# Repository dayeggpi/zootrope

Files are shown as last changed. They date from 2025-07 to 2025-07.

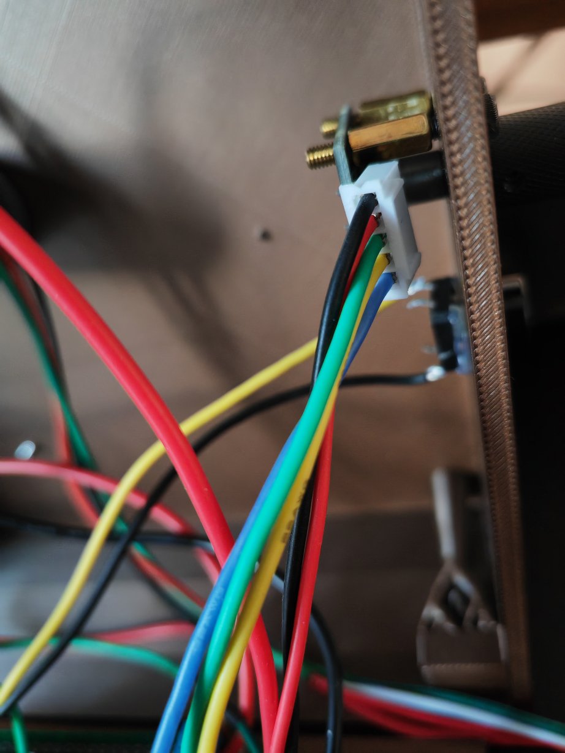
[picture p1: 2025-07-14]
images/rotary-wiring.jpg

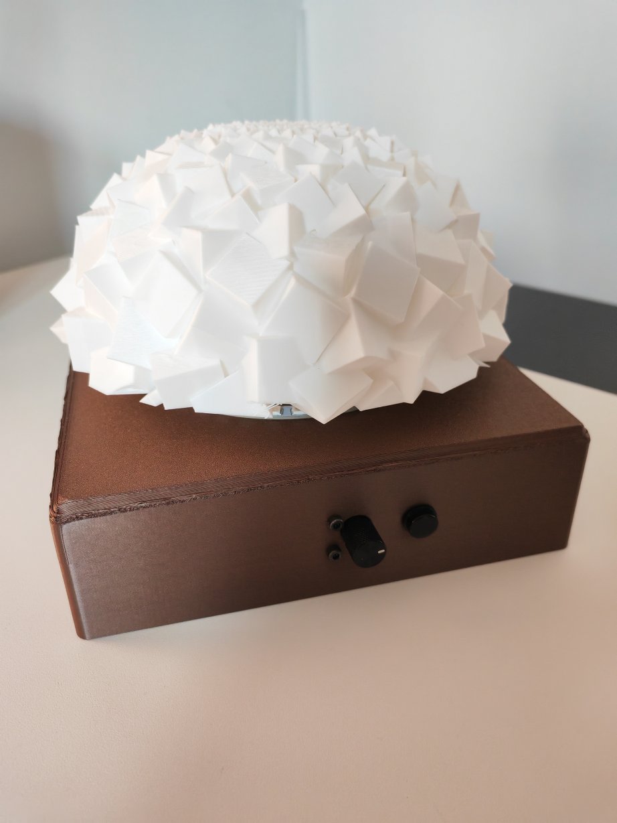
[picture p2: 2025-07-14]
images/final.jpg

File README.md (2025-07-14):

# zootrope
Build your own zootrope and phenakistoscope, a kinetic sculpture

# Keywords

- zootrope
- zoetrope
- phenakistiscope
- praxinoscope
- novatrope

# Showcase



More images in the "images" folder.
Note : the render on the gif might not do justice to the final product as the camera framerate of my phone isn't synchronized with the strobo effect of the leds to obtain the right effect...

Check out the videos in the links below to see how it should look like.

# Circuit

BOM: 
- MOSFET FQP30N06L or any logic N-channel (the "L" is important, for Logic)
- MABUCHI RS-385SH-2270 long shaft with gear (10T 5mm)
- KY-040 rotary encoder
- Arduino pro mini
- switch button
- WS2812B Led Ring 5V
- DC jack barrel
- ON/OFF switch button
- 1k resistor
- 100uf capacitor

Look at the circuit diagram to wire the motor properly. !! Careful !! that the mosfet in the circuit diagram is DSG, while the FQP30N06L is GDS (order of the legs), as per the datasheet attached for info).

For the leds, wire the 5V directly (NOT via the arduino) and the data to the arduino pin 10 (PMW).

The microswitch is a simple wiring (GND on one side, and arduino pin A0 on the other).

The KY-040 is also straight forward : GND to GND, + to 5V, CLK to arduino pin 3, DT to arduino pin 5, SW to arduino pin 6 as we need PMW pins.

# 3D

Print the box.stl, place the led ring in the middle, and fix the rotor with screws.

Add the DC jack barrel and the on/off switch on tone side, as well as the KY-040 rotary encoder and a swtich button on the other side.

Close the box with the lid and fix it to it.

# Code

Adjust code as needed for pins, for the following values:

```
// Motor settings
const int motorMinValue = 0;
const int motorMaxValue = 255;
const int motorStepValue = 1;

// Blink settings
const int blinkMinValue = 0;
const int blinkMaxValue = 5000;
const int blinkStepValue = 100;

int motorValue = 20;
int blinkValue = 2700;
#define NUM_LEDS 40
#define LED_PIN 10
int motorPin = 9; // The pin connected to the transistor base
```

Keep the arduino plugged to the computer, and check the serial monitor in Arduino IDE to see the values of the motor and blink that will bring the best zootrope effect, and then set these values as default in the code.

You might need an FTDI232 to send the code to the arduino.

# Usage

Place the 3D model on top of the gear (adjust the slicer settings so that the 3D model is as light as possible, no need to get a lot of infils, or max details).

Turn the circuit on, wait for rotor to spin at speed, the rotary encoder and click it to save the value of the motor speed. Then click the swtich button to switch to the led blink value, and use rotary encoder to adjust the values and click the rotary encoder to save the value (i.e. the switch button allows you to toggle the config of the motor speed or the led blinking frequency).

Note, if your rotor can turn as low as a few RPM (40/50/70), then you can also print phenakistoscope images that will display nicely.

# Go further and link/references

- https://www.youtube.com/watch?v=f3xNOfmQZW0
- https://www.youtube.com/watch?app=desktop&v=5BcFZdcoYD8
- https://www.youtube.com/watch?v=7v01Rgxuyc4
- https://www.youtube.com/watch?v=h0gyoMDzWwI
- https://www.instructables.com/Blooming-Zoetrope-Sculptures/
- https://hackaday.io/project/170379-3d-zoetrope
- https://www.printables.com/model/733786-zootrope-by-lfpoulain
- https://www.yembarwar.com/blog/zoetrope-vinyl
- https://publicdomainreview.org/collection/phenakistoscopes-1833/
- https://www.behance.net/search/projects/phenakistoscope

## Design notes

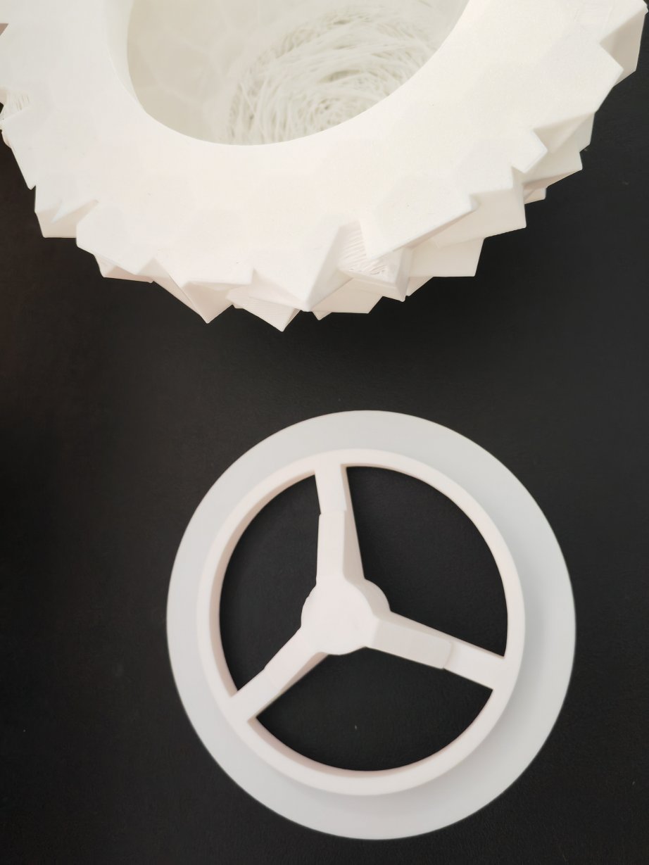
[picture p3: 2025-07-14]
images/base.jpg

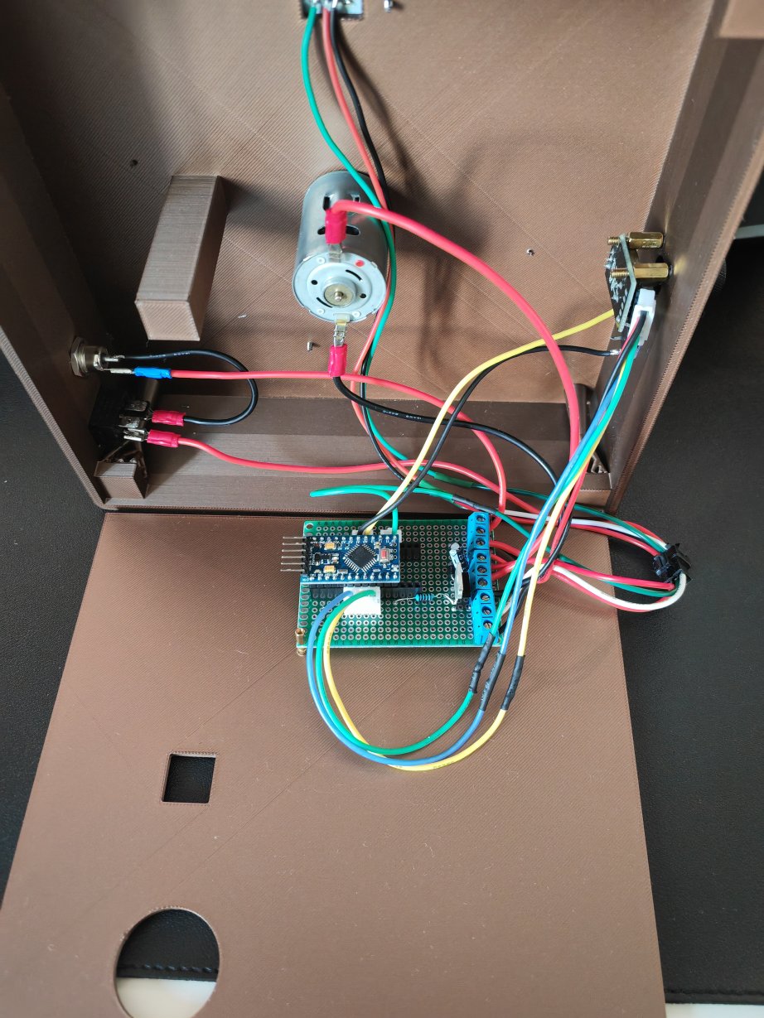
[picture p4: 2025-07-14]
images/inside.jpg

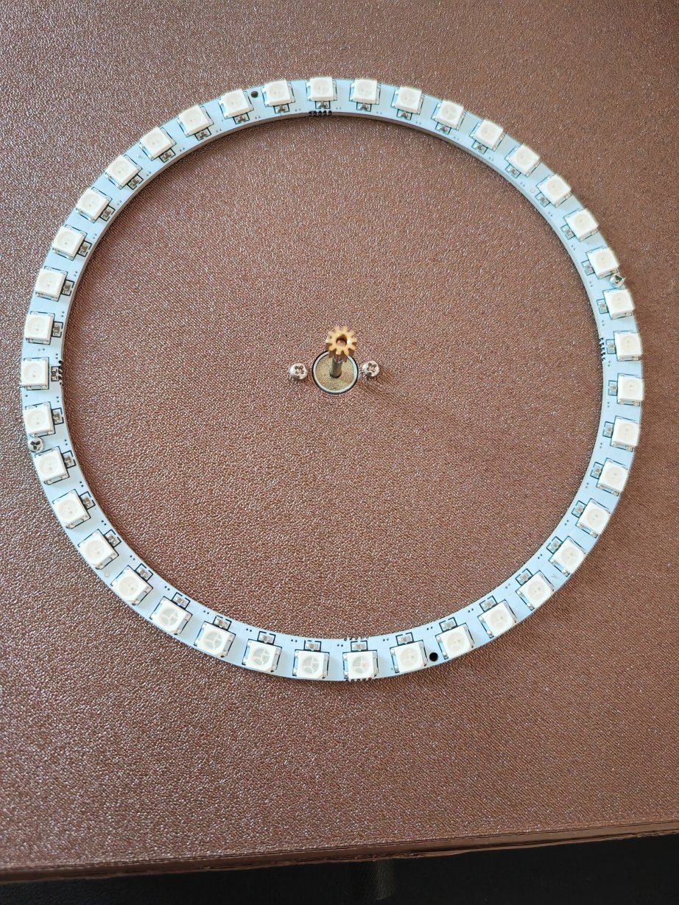
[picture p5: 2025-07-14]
images/circleled.jpg

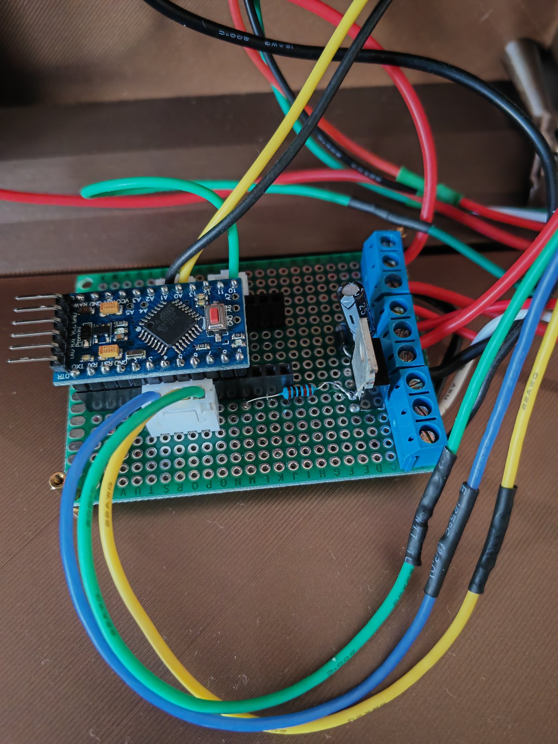
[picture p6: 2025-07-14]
images/closeup-circuit.jpg

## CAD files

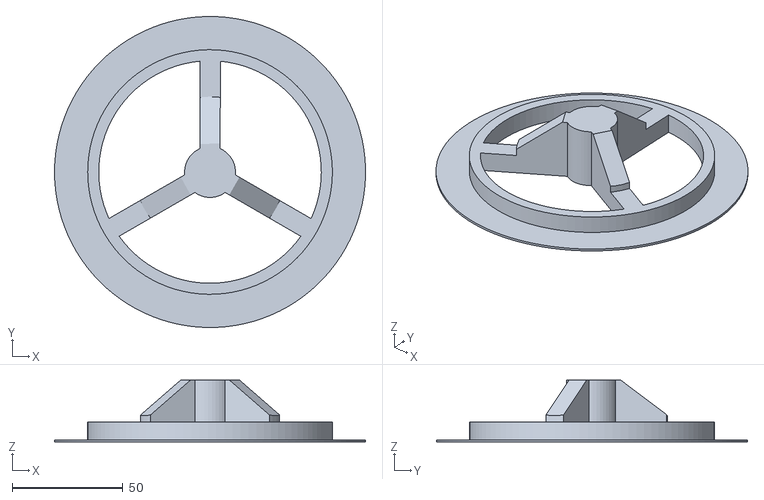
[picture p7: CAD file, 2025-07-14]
3D STL/base-with-gear.stl
140.5 x 140.5 x 28.0

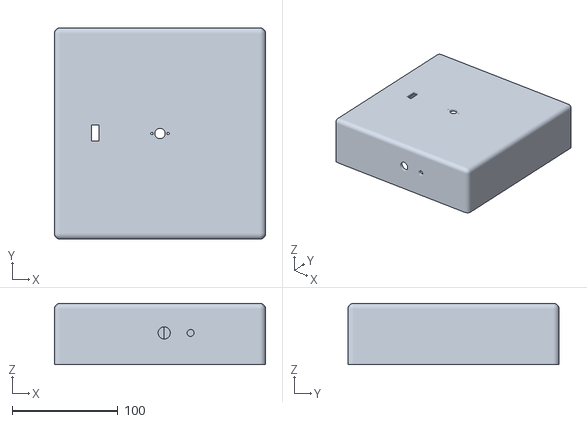
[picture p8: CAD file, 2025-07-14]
3D STL/box.stl
200.0 x 200.0 x 58.0

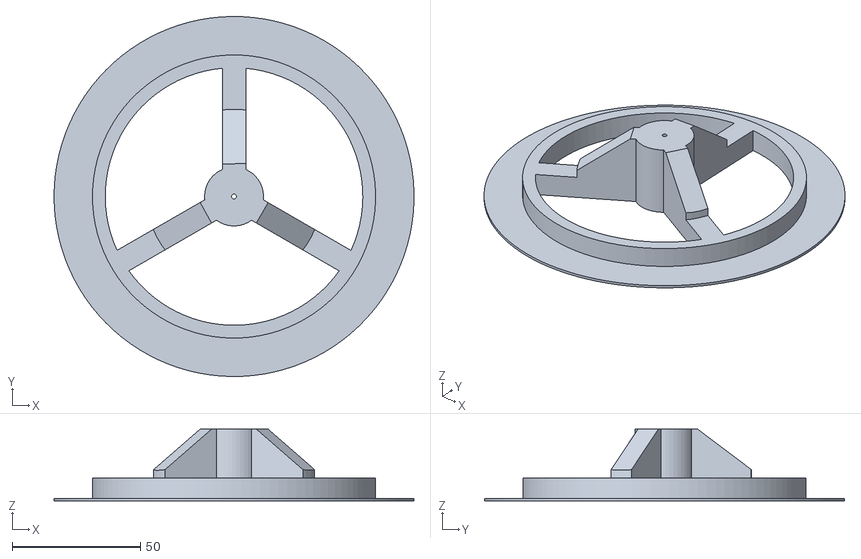
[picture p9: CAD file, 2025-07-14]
3D STL/base-simple-hole.stl
140.5 x 140.5 x 28.0

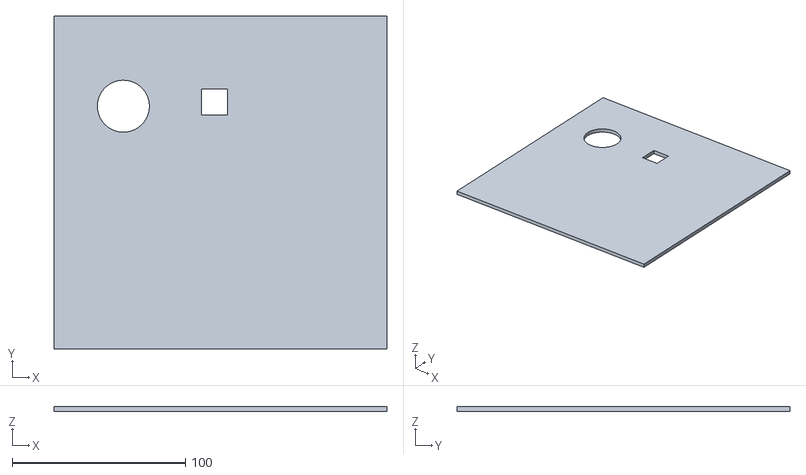
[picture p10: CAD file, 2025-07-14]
3D STL/close-lid.stl
192.0 x 192.0 x 3.00

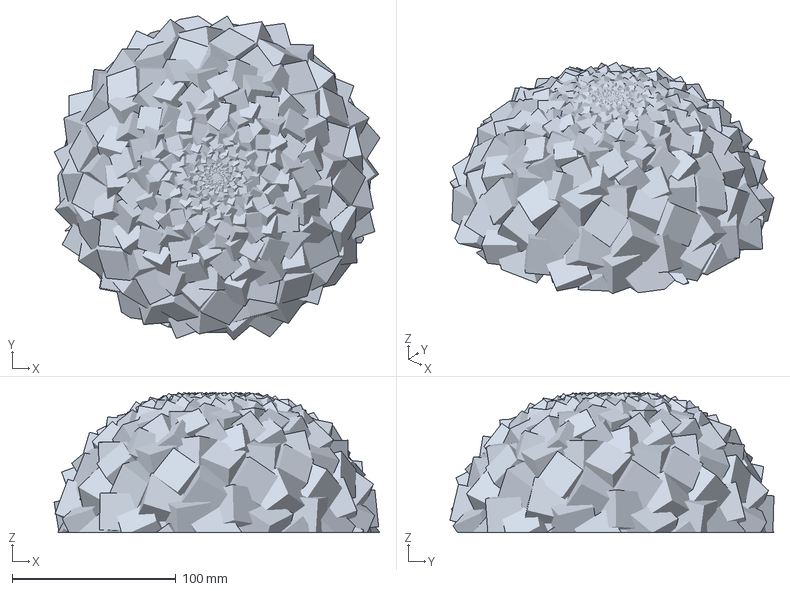
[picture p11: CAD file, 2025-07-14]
3D STL/shape.3mf
199.0 x 197.9 x 85.7 mm

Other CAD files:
3D STL/base-no-hole.3mf

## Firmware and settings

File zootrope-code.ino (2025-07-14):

#include <FastLED.h>
const int pinCLK    = 3;   // Encoder CLK
const int pinDT     = 5;   // Encoder DT
const int pinSW     = 6;   // Encoder push button
// const int pinSwitch = A0;   // Mode toggle button

// Motor settings
const int motorMinValue = 0;
const int motorMaxValue = 255;
const int motorStepValue = 1;

// Blink settings
const int blinkMinValue = 0;
const int blinkMaxValue = 5000;
const int blinkStepValue = 100;

int motorValue = 20;
int blinkValue = 2700;
int currentValue = 0;
bool settingMotor = true;  // true = motor, false = blink

int lastCLK = HIGH;

// Debounce for buttons and rotary
unsigned long lastDebounceSW = 0;
unsigned long lastDebounceSwitch = 0;
unsigned long lastEncoderMove = 0;
const unsigned long debounceDelay = 50;
const unsigned long encoderDebounce = 3; // ms between encoder changes
bool lastSWState = HIGH;
bool lastSwitchState = HIGH;

#define NUM_LEDS 40
#define LED_PIN 10
int motorPin = 9; // The pin connected to the transistor base
int speed = 200; // A value in the range [0..255] which represents the
int counter = 0;
int lastStateCLK = HIGH;
int currentStateCLK;
int strobeHz = 0;

const int rpm = 255;
const uint32_t rpm_us = 60000000 / rpm;

int tourminute = 0;

void setup() {
  delay(2000); // Wait 1 second for everything to stabilize
  pinMode(pinCLK, INPUT);
  pinMode(pinDT, INPUT);
  pinMode(pinSW, INPUT_PULLUP);
  pinMode(A0, INPUT_PULLUP);
  Serial.begin(9600);
  currentValue = motorValue;
  Serial.println("Mode: Motor value adjustment");
  Serial.print("Current value: ");
  Serial.println(currentValue);
  
  //motor
  pinMode(motorPin, OUTPUT);

  //led
  FastLED.addLeds<WS2812B, LED_PIN, GRB>(0, NUM_LEDS);
  FastLED.setMaxRefreshRate(0, false);
}

void loop() {
  // Rotary encoder logic with debounce - FIXED DIRECTION
  int newCLK = digitalRead(pinCLK);
  if (lastCLK == HIGH && newCLK == LOW) { // Falling edge
    if (millis() - lastEncoderMove > encoderDebounce) {
      int dtValue = digitalRead(pinDT);
      
      // Get current min/max/step values based on mode
      int minVal, maxVal, stepVal;
      if (settingMotor) {
        minVal = motorMinValue;
        maxVal = motorMaxValue;
        stepVal = motorStepValue;
      } else {
        minVal = blinkMinValue;
        maxVal = blinkMaxValue;
        stepVal = blinkStepValue;
      }
      
      // Fixed direction logic - clockwise always increases, counterclockwise always decreases
      if (dtValue == HIGH) {
        // Clockwise - increase value (don't wrap around at max)
        if (currentValue < maxVal) {
          currentValue += stepVal;
          if (currentValue > maxVal) currentValue = maxVal;
        }
      } else {
        // Counterclockwise - decrease value (don't wrap around at min)
        if (currentValue > minVal) {
          currentValue -= stepVal;
          if (currentValue < minVal) currentValue = minVal;
        }
      }
      
      Serial.print("Current value: ");
      Serial.println(currentValue);
      lastEncoderMove = millis();
    }
  }
  lastCLK = newCLK;

  // Rotary encoder button (SW) to validate value
  bool swState = digitalRead(pinSW);
  if (swState == LOW && lastSWState == HIGH && (millis() - lastDebounceSW) > debounceDelay) {
    lastDebounceSW = millis();
    if (settingMotor) {
      motorValue = currentValue;
      Serial.print("Motor value saved: ");
      Serial.println(motorValue);
    } else {
      blinkValue = currentValue;
      Serial.print("Blink value saved: ");
      Serial.println(blinkValue);
    }
  }
  lastSWState = swState;

  // Tactile switch (pin A0) to change mode
  bool switchState = digitalRead(A0);
  if (switchState == LOW && lastSwitchState == HIGH && (millis() - lastDebounceSwitch) > debounceDelay) {
    lastDebounceSwitch = millis();
    settingMotor = !settingMotor;
    if (settingMotor) {
      currentValue = motorValue;
      Serial.println("Mode: Motor value adjustment (0-255, step 5)");
    } else {
      currentValue = blinkValue;
      Serial.println("Mode: Blink value adjustment (0-5000, step 100)");
    }
    Serial.print("Current value: ");
    Serial.println(currentValue);
  }
  lastSwitchState = switchState;
  
  FastLED.showColor(CRGB::White);
  FastLED.showColor(CRGB::Black);
  static uint64_t next_flash_us = micros();
  if (blinkValue != 0)
    tourminute = 60000000 / (blinkValue);
  else
    tourminute = 0; // or another safe value

  if ((next_flash_us += tourminute) < micros())
    next_flash_us = micros();
  while (const uint64_t delay_us = next_flash_us - micros() < tourminute)
    delayMicroseconds(delay_us);

  //rotor
  analogWrite(motorPin, motorValue);
}
